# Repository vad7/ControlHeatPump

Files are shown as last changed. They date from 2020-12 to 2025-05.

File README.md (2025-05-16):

# ControlHeatPump
Контроллер теплового насоса

Версия 1.196.<br>
<br>
Проект "Народный контроллер" для тепловых насосов.<br>
Данное програмноое обеспечение предназначено для управления<br>
различными типами тепловых насосов для отопления и ГВС.<br>
<br>
Плата для контроллера, более продробно описана здесь: http://vad-7.blogspot.com/2021/04/HPboard.html
<br>
Гребер и БОМ лист в папке: Arduino DUE shield<br>
<br>
На плате:<br>
1. Разъемы для установки Arduino DUE R3<br>
2. Проводная сеть (W5500) для доступа к контроллеру через интернет<br>
3. Две раздельные линии для цифровых датчиков температуры DS18B20, одна из которых может быть 2-х проводной.<br>
4. Разъем для micro SD карты<br>
5. Флеш-память для веб морды<br>
6. Память 128кбайт для настроек и лога<br>
7. Часы с батарейкой CR2032<br>
8. Опора точного напряжения для аналоговых входов (нужно переключить режим на Arduino DUE)<br>
9. Подключение символьного дисплея LCD 16x2-20x4, доступен также графический Nextion.<br>
10. ЭРВ с униполярной катушкой<br>
11. 2 входа токовая петля 4-20мА<br>
12. 4 аналоговых входа с делителем напряжения<br>
13. 6 цифровых полностью изолированных входов с раздельным подключением изолированного источника напряжения.<br>
14. 2 аналоговых выхода 0-10V<br>
15. Выход на платы реле (до 12 реле)<br>
16. 1 высокоскоростной ШИМ<br>
17. 2 изолированных DC выхода<br>
18. 4 сериал порта<br>
19. 2 шины I2C<br>
20. 6 неизолированных многоцелевых (включая ШИМ) входов-выходов.<br>
21. Зуммер на 12V<br>
22. Разъем для 4-х кнопок.<br>
<br>
Размер 176x120 мм, Arduino DUE выступает на 16 мм.<br>
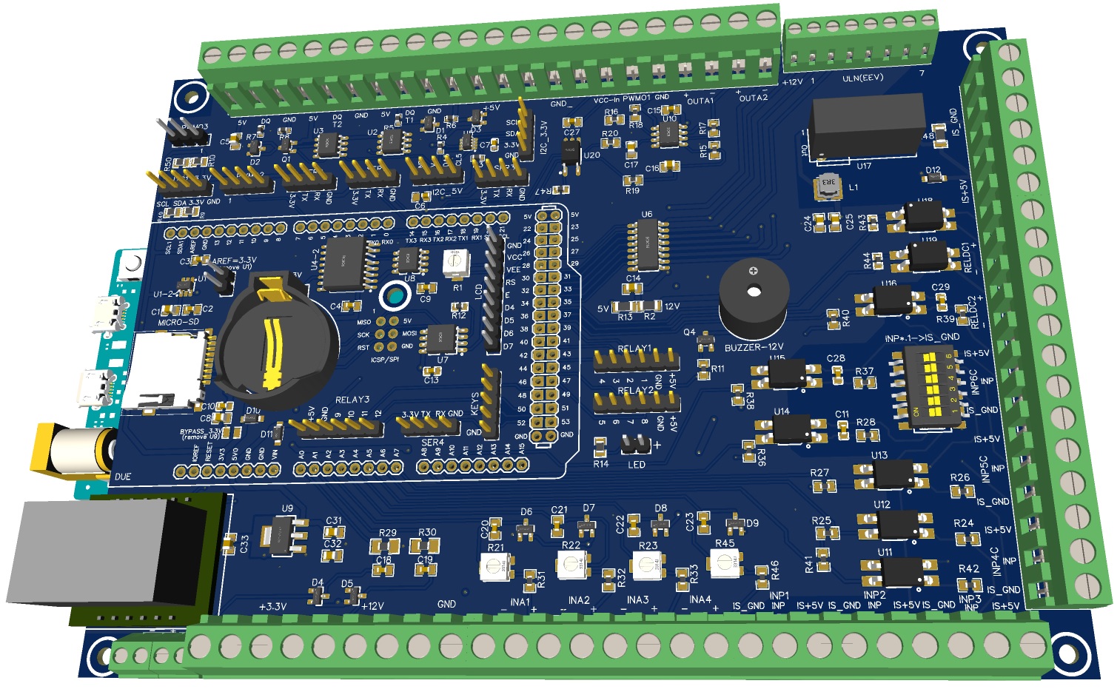
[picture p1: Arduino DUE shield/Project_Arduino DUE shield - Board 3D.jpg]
qr

<br>
<br>
1. Поддержка символьного дисплея 20x4 символов (LCD2004), может работать совместно с Nextion.<br>
2. ТН Воздух-Вода - полная поддержка, установка оборотов компрессора, ЭРВ.<br>
3. Ежесуточные реле - переключение по температуре и по ночному тарифу<br>
4. Дамп ячеек Modbus, загрузка файла дампа в устройство Modbus<br>
5. Частотник Vacon: управление вентилятором, настройка мощности, контроль температуры, авто-сброс ошибки связи<br>
6. Дисплей Nextion: описание ошибки ТН текстом на главном экране, отображение второго уличного датчика, исправление ошибок<br>
7. Исправление множества ошибок в функциях: EEV, WR, Vacon, COP, Pumps, web<br>
8. Корректировка ЭРВ при переходе отопление-бойлер<br>
9. Опция включения циркуляционного насоса ГВС по расписанию<br>
10. Возможность изменять аварийные границы датчиков температур через веб<br>
11. Ограничение оборотов компрессора по времени<br>
12. ГВС: использовать только тэн во время "расписание только для тэна"<br>
13. Не считать статистику с меткой "во время работы" в переходных моментах бойлер-отопление и при возврате масла<br>
14. Статистика - отдельно считается тэн бойлера<br>
15. Пересоздание stats файлов при ошибке последовательности или длине=0<br>
16. Исправление работы насосов в паузе<br>
17. Исправление синхронизации времени, запрет смены часов во время работы ТН<br>
18. Исправление скролбара в веб<br>
19. Опция запрещать смену конкретного расписания<br>
20. Исправление безопасного доступа через веб, из-за кэширования он не работал адекватно<br>
21. Опция продолжения отопления после нагрева бойлера, если внутри гистерезиса<br>
22. Отображение на веб о включении суточных реле<br>
23. Корректировка минимальной мощности ваттроутера в зависимости текущей мощности с MPPT<br>
24. Поддержку двунаправленного электро-счетчика DDS238-2 ZN/S<br>
25. Настройки насосов отопления и дополнительного тэна перенесены в профили<br>
26. Новый режим работы дополнительного тэна на выходе ТН - интеллектуальный, теперь их три: по дому, по улице, интеллектуально<br>
27. Температура цели бойлера на схеме<br>
28. Корректировка датчиков WiFi (esp8266)<br>
29. Нагрев бойлера во время отсутствия электричества, если есть солнце<br>
30. Перенос настройки выключения насоса после останова компрессора в профили, отдельная задача по управлению насосами, чтобы была возможность контроля температур цели.<br>
31. Автопереключение режима работы - Отопление / Охлаждение<br>
32. Возможность использовать несколько периодов включения одного и того же ежесуточного реле.<br>
33. Возможность задать дополнительно любой датчик температуры как цель отопления. Расписание по часам контроля этих датчиков для каждого профиля.<br>
34. Догрев бойлера тэном во время паузы компрессора и низкой температуры или когда не смог нагреть с первого раза.<br>
35. Управление теплым полом по датчикам теплого пола. Два режима - по превышению на заданную дельту целевой температуры или по целевой температуре датчика.<br>
36. Старт нагрева по минимальной температуре подачи.<br>
37. Максимальная температура цели для принудительного останова цикла нагрева, если по другим датчикам еще нужно греть.  <br>
38. Поддержка частотников Danfoss VLT, Danfoss Micro Drive FC-51.<br>
39. Управления дополнительным солнечным подкачивающим инвертором (через реле).<br>
40. Подсчет потребления по дневному/ночному тарифу раздельно, опциональное.<br>

<br><br>

Подробное обсуждение проекта на форуме: <br>
https://www.forumhouse.ru/threads/492563/

Скриншеты веб-интерфейса:

Состояние
Схема
ЭРВ
Настройки
Расписание
Датчики
Реле
Инвертор
RTOS
Графики
Графический лог
Статистика
Ваттроутер

Выносной экран Nextion:

Nextion Main
Nextion Scheme
Nextion Heat

Символьный дисплей LCD2004:



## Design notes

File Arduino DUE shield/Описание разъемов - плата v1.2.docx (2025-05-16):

Входы-выходы НК

№: 1 2 3 4 5 6 7 8 9 10

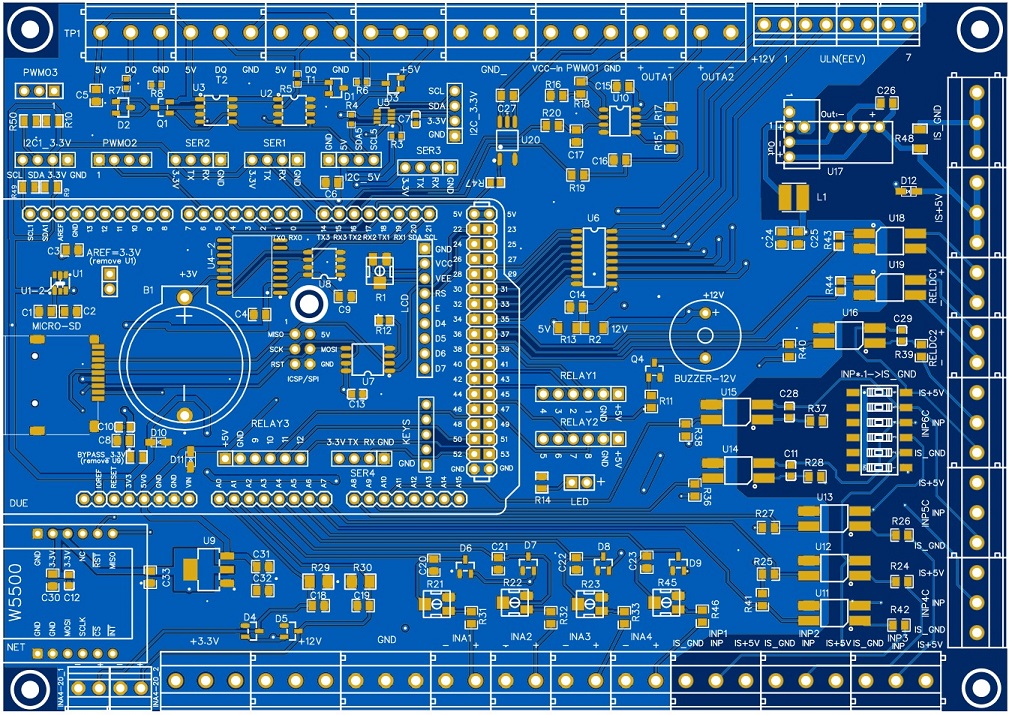
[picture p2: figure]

11

12

13

*

14

MicroSD

15

16

LAN 17

29 28 27 26 25 24 23 22 21 20 19 18

Винтовые разъемы по периметру платы:

1. Датчики температуры DS18B20, двухпроводная или трехпроводная линия (Шина 2)
2. Датчики температуры DS18B20, трехпроводная линия (Шина 1)
3. Датчики температуры DS18B20, трехпроводная линия (Шина 1)
4. Выходы +5V
5. GND (-)
6. Выход изолированный PWM, максимальный ток 8 mA (D5)
7. Выход аналоговый 0-10V (D2)
8. Выход аналоговый 0-10V (D3)
9. ЭРВ (ULN2003), слева на право: +5V или +12V (* - в зависимости от перемычки), D29, D30, D31
10. ЭРВ (ULN2003), слева на право: D32, D33, D34, D35
11. Выход изолированный -5V (GND)
12. Выход изолированный +5V, 1W
13. Реле постоянного тока (оптрон), макс +80V, 50 mA (D36)
14. Реле постоянного тока (оптрон), макс +80V, 50 mA (D37)
15. Вход цифровой изолированный со сглаживающим конденсатором (D38)
16. Вход цифровой изолированный со сглаживающим конденсатором (D64)
17. Вход цифровой изолированный со сглаживающим конденсатором (D63)
18. Вход цифровой изолированный (D62)
19. Вход цифровой изолированный (D61)
20. Вход цифровой изолированный (D60)
21. Вход аналоговый регулируемый R45 (A5/AD2)
22. Вход аналоговый регулируемый R23 (A4/AD3)
23. Вход аналоговый регулируемый R22 (A3/AD4)
24. Вход аналоговый регулируемый R21 (A2/AD5)
25. GND (-)
26. Вход/Выходы +12V
27. Выходы +3.3V
28. Вход аналоговый, токовая петля 4-20 мА, 75 Ом (A1/AD6)
29. Вход аналоговый, токовая петля 4-20 мА, 75 Ом (A0/AD7)

Переключатели INP*.1->IS_GND замыкают выводы IS_GND разъемов №15 - №20 (сверху вниз) на изолированный -5V (GND).

Разъемы на плате:

RELAY1 – Выход на плату реле, 3.3V, контакты 1-4 (D39, D40, D41, D42)

RELAY2 – Выход на плату реле, 3.3V, контакты 5-8 (D44, D45, D46, D47)

RELAY3 – Выход на плату реле, 3.3V, контакты 9-12 (D48, D49, D50, D51)

Платы реле 5V - включение высоким уровнем (High Level Trigger)

KEYS – Кнопки, снизу вверх (GND, D66, D67, D68, D69)

LCD – Цифровой дисплей 20x4 символов, 5V, R1 – регулировка контраста

LED – Зеленый светодиод

SER1 – Порт Serial3, 3.3V

SER2 – Порт Serial2, 3.3V

SER3 – Порт Serial1, 3.3V

SER4 – Порт Serial4, 3.3V

I2C_3.3V – Шина I2C 3.3V (I2C)

I2C_5V – Шина I2C 5V (I2C)

I2C1_3.3V – Вторая шина I2C 3.3V (I2C1)

PWM02 – Выходы/Входы МК 3.3V, 9 мА, доступен PWM (GND, D6, D7, D9)

PWM03 – Выходы/Входы МК 3.3V, 9 мА (D13 – 3 мА), доступен PWM (D11, D12, D13[LED])

B1 – Батарейка CR2032, 3V

Датчики токовая петля 4-20 мА 12V подключаются так:

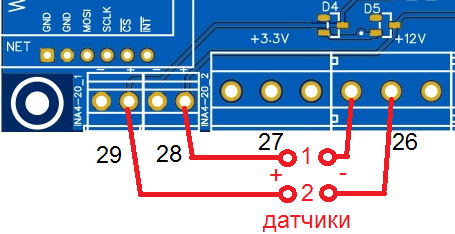
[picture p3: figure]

Доработка китайской платы Arduino DUE R3:

1. Припять резистор поверхностного монтажа (0603 размер) номиналом 10 кОм между ERASE линией и + 3,3В (на ножки транзистора).

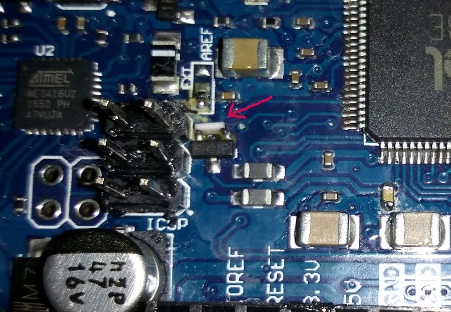
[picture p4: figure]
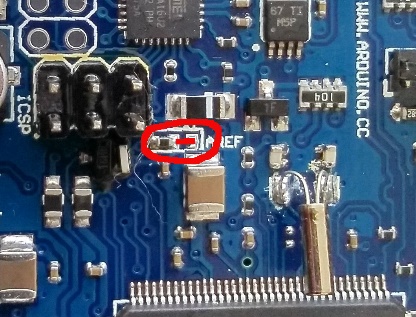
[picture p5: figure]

2. Перепаять перемычку AREF с левых контактов на правые – внешняя опора AREF.

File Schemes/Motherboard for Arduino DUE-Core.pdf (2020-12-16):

Платы 100x100мм.
Главная плата питается от 5V. Для аналогового выхода есть возможность подключить другое напряжение.
На плате места для:
1. платы часов (ZS_042)
2. платы сети W5500 lite (USR-ES1)
3. платы MicroSD 5V
4. разъем MicroSD
5. 3-х узких плат RS485 - TTL или других Serial-устройств.
6. 2 платы для датчиков температуры DS18B20 или других I2C устройств
7. дисплея LCD2004 (1602)
8. 4-х кнопок
9. Вторая шина I2C.

Входы-выходы:
1. два токовых входа (4-20 мА)
2. три аналоговых входа с подстройкой
3. два аналоговых выхода (LM358)
4. 18 цифровых выходов, включая 7 от ULN2003 для ЭРВ
5. 6 цифровых входов
6. Выход 5V через транзистор для пищалки, сирены или т. п.
Клеммники с шагом 5мм (KF128/129-5.08), на пищалку с шагом 3.5мм (KF350-3.5)

Плата реле реле подключается 20 пиновым двурядным шлейфом с шагом 2.54 мм (JTAG 2.54mm 20 pin).
На плату подается с внешнего источника высокое напряжение (12-24V и/или 5V) от них питаются ULN и реле.
На плате:
1. 6 развязанных через оптрон цифровых входа (клеммник KF350-3.5)
2. 5 твердотельных реле: оптосимистор + симистор BTA16 (16A), один можно воткнуть BTA41 (41A). (KF129-5.08)
3. 1 обычное реле на 16A, переключающие контакты (Omron G2RL-1-E или аналог) (KF129-5.08)
4. два выхода через оптрон, один можно сделать аналоговым через PWM. (KF350-3.5)
5. ULN2003 для управления ЭРВ или типа того (KF350-3.5)

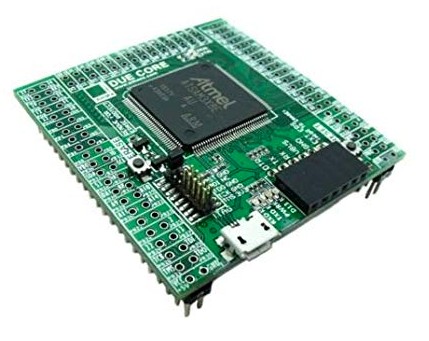
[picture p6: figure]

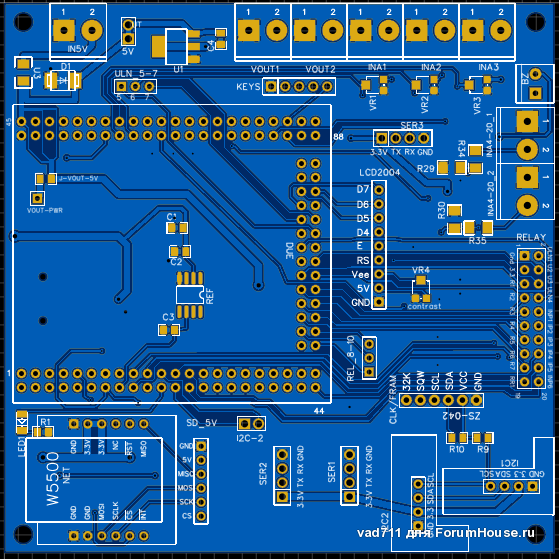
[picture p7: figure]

Плата реле:

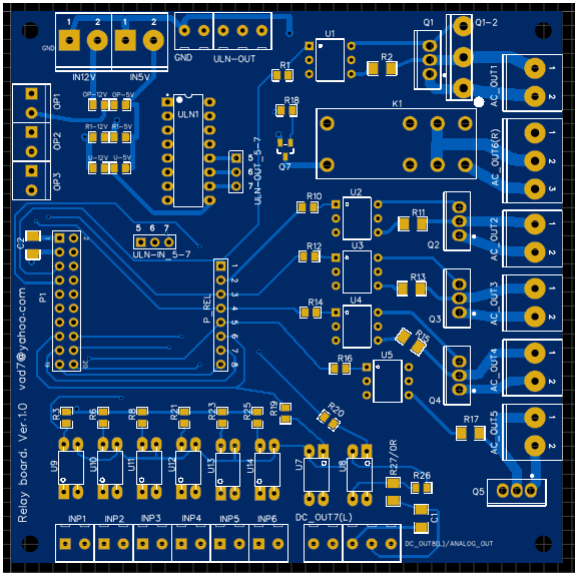
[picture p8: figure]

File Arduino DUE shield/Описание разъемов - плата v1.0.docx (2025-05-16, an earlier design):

Входы-выходы НК

№: 1 2 3 4 5 6 7 8 9 10 11

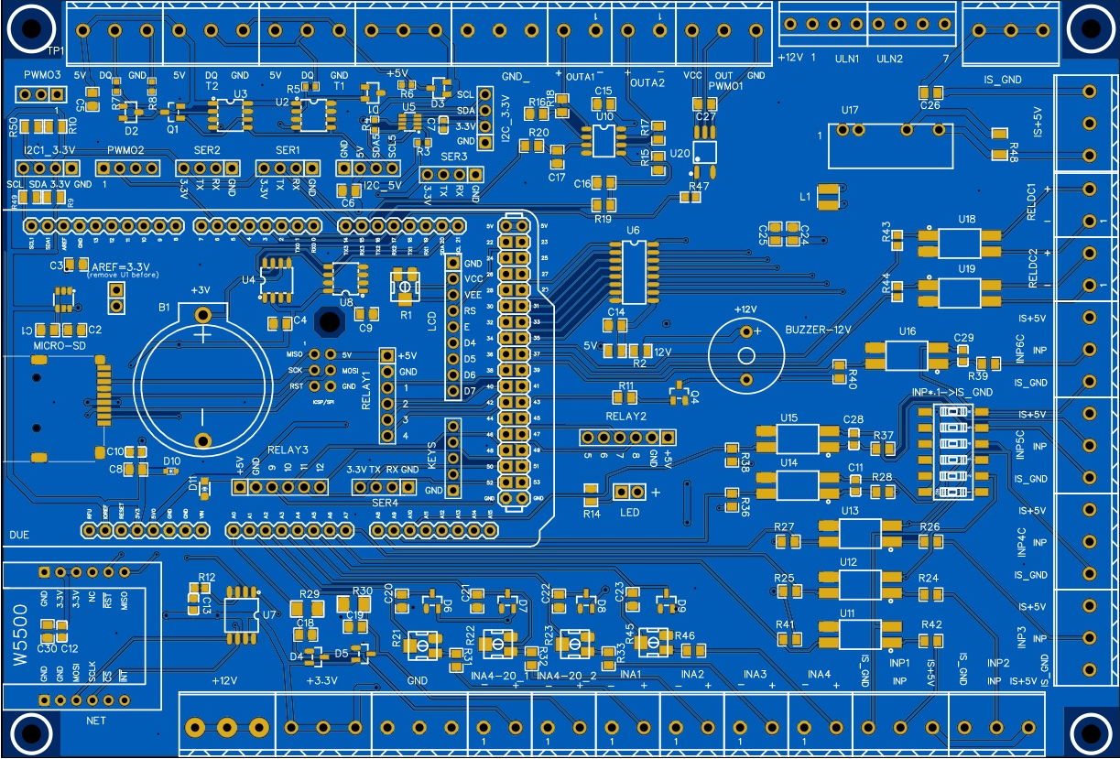
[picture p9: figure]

12

13

14

*

15

MicroSD

16

17

LAN 18

29 28 27 26 25 24 23 22 21 20 19

Винтовые разъемы по периметру платы:

1. Датчики температуры DS18B20, двухпроводная или трехпроводная линия (Шина 2)
2. Датчики температуры DS18B20, трехпроводная линия (Шина 1)
3. Датчики температуры DS18B20, трехпроводная линия (Шина 1)
4. Выходы +5V
5. GND (-)
6. Выход аналоговый 0-10V (D2)
7. Выход аналоговый 0-10V (D3)
8. Выход изолированный PWM, максимальный ток 8 mA (D5)
9. ЭРВ (ULN2003), слева на право: +5V или +12V (* - в зависимости от перемычки), D29, D30, D31
10. ЭРВ (ULN2003), слева на право: D32, D33, D34, D35
11. Выход изолированный -5V (GND)
12. Выход изолированный +5V, 1W
13. Реле постоянного тока (оптрон), макс +80V, 50 mA (D36)
14. Реле постоянного тока (оптрон), макс +80V, 50 mA (D37)
15. Вход цифровой изолированный со сглаживающим конденсатором (D38)
16. Вход цифровой изолированный со сглаживающим конденсатором (D64)
17. Вход цифровой изолированный со сглаживающим конденсатором (D63)
18. Вход цифровой изолированный (D62)
19. Вход цифровой изолированный (D61)
20. Вход цифровой изолированный (D60)
21. Вход аналоговый регулируемый R45 (A5/AD2)
22. Вход аналоговый регулируемый R23 (A4/AD3)
23. Вход аналоговый регулируемый R22 (A3/AD4)
24. Вход аналоговый регулируемый R21 (A2/AD5)
25. Вход аналоговый, токовая петля 4-20 мА, 75 Ом (A1/AD6)
26. Вход аналоговый, токовая петля 4-20 мА, 75 Ом (A0/AD7)
27. GND (-)
28. Выходы +3.3V
29. Вход/Выходы +12V

Переключатели INP*.1->IS_GND замыкают выводы IS_GND разъемов №15 - №20 (сверху вниз) на изолированный -5V (GND).

Разъемы на плате:

RELAY1 – Выход на плату реле, 3.3V, контакты 1-4 (D39, D40, D41, D42)

RELAY2 – Выход на плату реле, 3.3V, контакты 5-8 (D44, D45, D46, D47)

RELAY3 – Выход на плату реле, 3.3V, контакты 9-12 (D48, D49, D50, D51)

Платы реле 5V - включение высоким уровнем (High Level Trigger)

KEYS – Кнопки, снизу вверх (GND, D66, D67, D68, D69)

LCD – Цифровой дисплей 20x4 символов, 5V, R1 – регулировка контраста

LED – Зеленый светодиод

SER1 – Порт Serial3, 3.3V

SER2 – Порт Serial2, 3.3V

SER3 – Порт Serial1, 3.3V

SER4 – Порт Serial4, 3.3V

I2C_3.3V – Шина I2C 3.3V (I2C)

I2C_5V – Шина I2C 5V (I2C)

I2C1_3.3V – Вторая шина I2C 3.3V (I2C1)

PWM02 – Выходы/Входы МК 3.3V, 9 мА, доступен PWM (GND, D6, D7, D9)

PWM03 – Выходы/Входы МК 3.3V, 9 мА (D13 – 3 мА), доступен PWM (D11, D12, D13[LED])

B1 – Батарейка CR2032, 3V

Датчики токовая петля 4-20 мА 12V подключаются так:

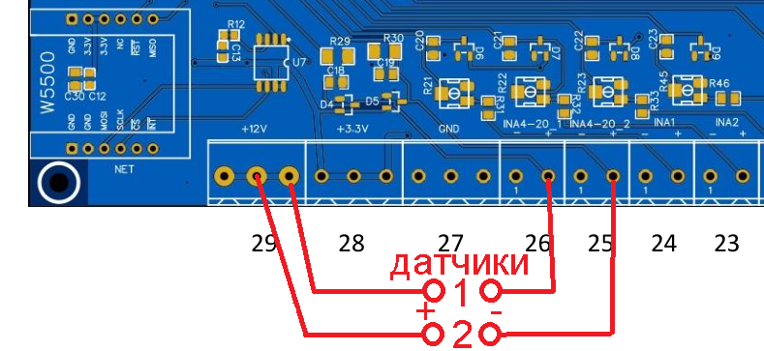
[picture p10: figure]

Доработка китайской платы Arduino DUE R3:

1. Припять резистор поверхностного монтажа (0603 размер) номиналом 10 кОм между ERASE линией и + 3,3В (на ножки транзистора).


2. Перепаять перемычку AREF с левых контактов на правые – внешняя опора AREF.

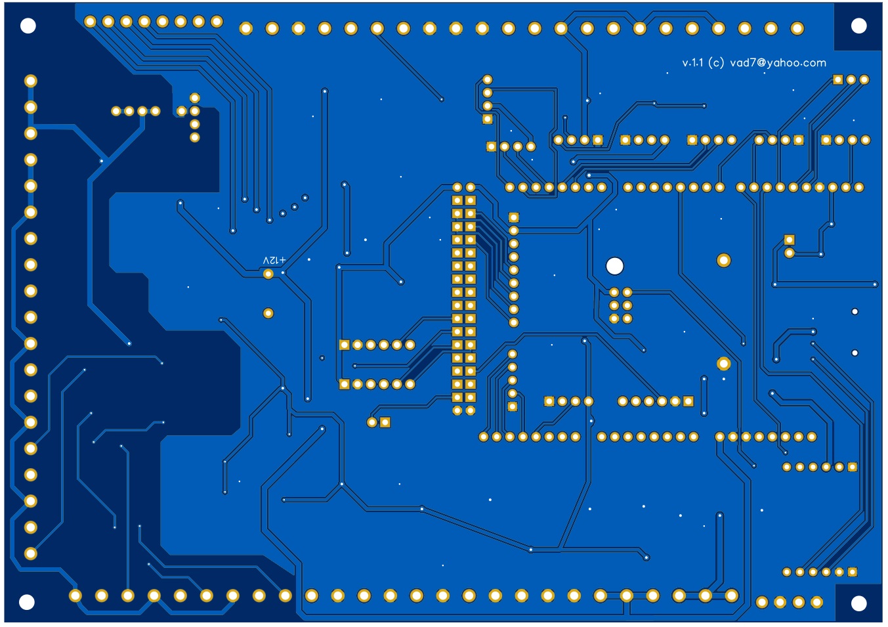
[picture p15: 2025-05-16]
Arduino DUE shield/Project_Arduino DUE shield - Board 2D_2.jpg

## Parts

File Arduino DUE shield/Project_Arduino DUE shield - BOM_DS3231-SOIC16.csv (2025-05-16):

ID | Name | Designator | Footprint | Quantity | Manufacturer Part | Manufacturer | Supplier | Supplier Part | Mounted | LCSC Assembly | JLCPCB SMD | Assembly Type | Paste Type
1 | CR2032-BS-2-1 | B1 | BAT-TH_BS-2-1 | 1 | BS-2-1 | Q&J | LCSC | C70376
2 | TMB12A12 | BUZZER-12V | BUZ-TH_BD12.0-P7.60-D0.6-FD | 1 | TMB12A12 | HNDZ | LCSC | C96079 |  | Yes
3 | 10u | C5 | C_805 | 1 | CL21A106KAYNNNE | SAMSUNG | LCSC | C15850 | Yes
4 | 0.1u | C6,C7 | C0603 | 2 | CC0603KRX7R9BB104 | YAGEO | LCSC | C14663 | Yes
5 | 0.1u | C2,C3,C4,C9,C10,C12,C13,C15,C26,C27 | C0603 | 10 | CC0603KRX7R9BB104 | YAGEO | LCSC | C14663
6 | 10u | C1,C8,C14,C16,C17,C24,C25,C30,C31,C32,C33 | C_805 | 11 | CL21A106KAYNNNE | SAMSUNG | LCSC | C15850
7 | 0.01u | C11,C18,C19,C20,C21,C22,C23,C28,C29 | C0603 | 9 | 0603B103K500NT | FH | LCSC | C57112
8 | PACDN042Y3R | D1,D2,D3 | SOT-23-3_L3.0-W1.7-P0.95-LS2.9-BR | 3 | PACDN042Y3R | ON Semicon | LCSC | C233486 |  | Yes
9 | BAT54SLT1G | D4,D5,D6,D7,D8,D9 | SOT-23_L2.9-W1.3-P1.90-LS2.4-BR | 6 | BAT54SLT1G | ON | LCSC | C19726 |  |  | Yes
10 | UCLAMP3301H.TCT | D10 | SOD123-SOD523 | 1 | UCLAMP3301H.TCT | SEMTECH | LCSC | C117558 |  | Yes | Yes | smtWeld | expand
11 | DESD5V0U1BA-7 | D11,D12 | SOD123-SOD523 | 2 | DESD5V0U1BA-7 | Diodes Incorporated | LCSC | C460442
12 | PA_DUE_BRD | DUE | PA_DUE 1 HOLE | 1 | ?
13 | A2541WV-4P | I2C1_3.3V,I2C_3.3V | HDR-TH_4P-P2.54-V I2C 3.3V | 2 | A2541WV-4P | Changjiang Connectors | LCSC | C225479 |  | Yes
14 | A2541WV-4P | I2C_5V | HDR-TH_4P-P2.54-V I2C 5V | 1 | A2541WV-4P | Changjiang Connectors | LCSC | C225479 |  | Yes
15 | KF128L-5.08-2P | INA1,INA2,INA3,INA4,RELDC1,RELDC2 | CONN-TH_P5.08_KF128L-5.08-2P SIGN | 6 | KF128L-5.08-2P | Cixi Kefa Elec | LCSC | C474940 |  | Yes
16 | KF128L-3.5-2P | INA4-20_1,INA4-20_2 | CONN-TH_P3.50_KF128L-3.5-2P SIGN | 2 | KF128L-3.5-2P | Cixi Kefa Elec | LCSC | C474930 |  | Yes |  | manualWeld | expand
17 | KF128L-5.08-3P | INP1,INP2,INP3,INP4C,INP5C,INP6C | CONN-TH_3P-P5.08_KF128L-5.08-3P INP | 6 | KF128L-5.08-3P | Cixi Kefa Elec | LCSC | C474941 |  | Yes
18 | EM-06-Q | INP*.1->IS_GND | SW-SMD_12P-L15.1-W6.0-P2.54-LS9.8 | 1 | EM-06-Q | Diptronics | LCSC | C501580 |  | Yes |  | smtWeld | expand
19 | KF128L-5.08-3P | +3.3V,+5V,+12V,GND,GND_,IS+5V,IS_GND,PWMO1 | CONN-TH_3P-P5.08_KF128L-5.08-3P | 8 | KF128L-5.08-3P | Cixi Kefa Elec | LCSC | C474941 |  | Yes
20 | A2541WV-5P | KEYS | HDR-TH_5P-P2.54-V | 1 | A2541WV-5P | Changjiang Connectors | LCSC | C225480 |  | Yes
21 | 10uH | L1 | IND-SMD_3.0-4.0W | 1 | FNR4018S100MT | cjiang | LCSC | C167808
22 | PZ254V-11-09P | LCD | HDR-TH_9P-P2.54-V-M LCD | 1 | PZ254V-11-09P | XFCN | LCSC | C492408 |  | Yes
23 | TF-01A | MICRO-SD | TF-SMD_TF-01A | 1 | TF-15×15 | SOFNG | LCSC | C111196
24 | W5500 module | NET | W5500_MODULE | 1 | ?
25 | KF128L-5.08-2P | OUTA1,OUTA2 | CONN-TH_P5.08_KF128L-5.08-2P SIGN | 2 | KF128L-3.5-2P | Cixi Kefa Elec | LCSC | C474930 |  | Yes
26 | A2541WV-4P | PWMO2 | HDR-TH_4P-P2.54-V | 1 | A2541WV-4P | Changjiang Connectors | LCSC | C225479 |  | Yes
27 | A2541WV-3P | PWMO3 | HDR-TH_3P-P2.54-V-M | 1 | A2541WV-3P | Changjiang Connectors | LCSC | C225478 |  | Yes
28 | BSS84LT1G | Q1 | SOT-23-3_L2.9-W1.6-P1.90-LS2.8-BR | 1 | LBSS84LT1G | LRC | LCSC | C8492 |  | Yes | Yes
29 | BC817-25LT1G | Q4 | SOT-23-3_L2.9-W1.6-P1.90-LS2.8-BR | 1 | BC817-25LT1G | ON | LCSC | C82635 |  | Yes | Yes
30 | 10K | R1,R21,R22,R23,R45 | RES-ADJ-SMD_3314J | 5 | 3314J-1-103E | BOURNS | LCSC | C36376 |  | Yes
31 | 3.9k | R3,R4 | R0603 | 2 | 0603WAF3901T5E | UniOhm | LCSC | C23018 | Yes
32 | 5 | R5,R6,R7,R8 | R0603 | 4 | 0603WAF510KT5E | UniOhm | LCSC | C25197
33 | 1k | R9,R10,R49,R50 | R0805 | 4 | 0603WAF1001T5E | UniOhm | LCSC | C21190
34 | 10K | R11 | R0603 | 1 | 0603WAF1002T5E | UniOhm | LCSC | C25804
35 | 10k | R15,R16,R19,R20 | R0603 | 4 | 0603WAF1002T5E | UniOhm | LCSC | C25804
36 | 22k | R17,R18 | R0603 | 2 | 0603WAF2202T5E | UniOhm | LCSC | C31850
37 | 75 | R29,R30 | R0805 | 2 | 0805W8F750JT5E | UniOhm | LCSC | C20638
38 | 6.8k | R31,R32,R33,R46 | R0603 | 4 | 0603WAF6801T5E | UniOhm | LCSC | C23212
39 | 4.7k | R25,R27,R36,R38,R40,R41 | R0603 | 6 | 0603WAF4701T5E | UniOhm | LCSC | C23162
40 | 1k | R12,R24,R26,R28,R37,R39,R42,R43,R44 | R0603 | 9 | 0603WAF1001T5E | UniOhm | LCSC | C21190
41 | 330 | R14,R47 | R0603 | 2 | 0603WAF3300T5E | UniOhm | LCSC | C23138
42 | 300 | R48 | R1206 | 1 | 1206W4F3000T5E | UniOhm | LCSC | C17887 |  | Yes | Yes
43 | Header-Male-2.54_1x6 | RELAY1 | HDR-TH_6P-P2.54-V R5V1 | 1 | Header-Male-2.54_1x6 | BOOMELE | LCSC | C37208 |  | Yes
44 | Header-Male-2.54_1x6 | RELAY2 | HDR-TH_6P-P2.54-V R5V2 | 1 | Header-Male-2.54_1x6 | BOOMELE | LCSC | C37208 |  | Yes
45 | Header-Male-2.54_1x6 | RELAY3 | HDR-TH_6P-P2.54-V R5V3 | 1 | Header-Male-2.54_1x6 | BOOMELE | LCSC | C37208 |  | Yes
46 | A2541WV-4P | SER1,SER2,SER3,SER4 | HDR-TH_4P-P2.54-V SERIAL | 4 | A2541WV-4P | Changjiang Connectors | LCSC | C225479 |  | Yes
47 | KF128L-5.08-3P | T1,T2,TP1 | CONN-TH_3P-P5.08_KF128L-5.08-3P DS18B20 | 3 | KF128L-5.08-3P | Cixi Kefa Elec | LCSC | C474941 |  | Yes
48 | REF3030AIDBZR | U1-2 | SOT-23-3_L2.9-W1.6-REF | 1 | REF3030AIDBZR | TI | LCSC | C38423 |  |  | Yes | smtWeld | recommend
49 | DS2482S-100+TR | U2,U3 | SOIC-8_L4.9-W3.9-P1.27-LS6.0-BL | 2 | DS2482S-100+T&R | MAXIM | LCSC | C143306 |  | Yes | Yes
50 | DS3231M+TRL | U4-2 | SOIC-16_L10.3-W7.5-P1.27-LS10.3-BL NO_UNUSED_PIN | 1 | DS3231M+TRL | MAXIM | LCSC | C37663
51 | MAX3373EEKA+T | U5 | SOT-23-8_L3.0-W1.7-P0.65-LS2.8-TL THIN PADS | 1 | MAX3373EEKA+T | Maxim Integrated | LCSC | C116658 |  | Yes | Yes
52 | ULN2003D1013TR | U6 | SOIC-16_L9.9-W3.9-P1.27-LS6.0-BL | 1 | ULN2003ADR | TI | LCSC | C7512 |  | Yes | Yes
53 | MX25L3206EM2I-12G | U7 | SOIC-8_L5.3-W5.3-P1.27-LS8.0-BL | 1 | MX25L3206EM2I-12G | Micronix | LCSC | C16142 |  | Yes | Yes
54 | M24M01-RMN6TP | U8 | SOIC-8_L4.9-W3.9-P1.27-LS6.0-BL | 1 | M24M01-RMN6TP | STMicroelectronics | LCSC | C79990 |  | Yes | Yes
55 | LM1117MPX-3.3/NOPB | U9 | SOT-223-3_L6.5-W3.4-P2.30-LS7.0-BR | 1 | LM1117IMPX-3.3/NOPB | TI | LCSC | C23984 |  | Yes | Yes | smtWeld | expand
56 | LM358DR2G | U10 | SOIC-8_L5.0-W4.0-P1.27-LS6.0-BL | 1 | LM358DR2G | ON | LCSC | C7950 |  | Yes | Yes
57 | PC817X3NIP1B | U11,U12,U13,U14,U15,U16,U18,U19 | OPTO-SMD-4_L4.6-W6.5-P2.54_SOP-4-L3.9-W4.4 | 8 | EL357N(C)(TA)-G | EVERLIGHT | LCSC | C29981 |  |  | Yes
58 | IF1205S-2W | U17 | PWRM-TH_L11.6-19.6 | 1 | IF1205S-2W | Bothhand Enterprise | LCSC | C494963
59 | TLP104(TPL,E | U20 | SOP-6_5P-L4.4-W3.6-P1.27-LS7.0-BR-PE2 | 1 | TLP104(TPL,E | TOSHIBA | LCSC | C48236 |  | Yes | Yes
60 | KF128L-3.5-2P | ULN(EEV),ULN(EEV)1,ULN(EEV)2,ULN(EEV)3 | CONN-TH_P3.50_KF128L-3.5-2P CORR | 4 | KF128L-3.5-2P | Cixi Kefa Elec | LCSC | C474930 |  | Yes |  | manualWeld | expand

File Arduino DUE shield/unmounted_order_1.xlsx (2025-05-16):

R2,R13 | 0 | R1206 | Part Number:0 footprint name:R1206 [string length must be less or equal than 1 character] | 2
AREF=3.3V,LED | A2541WV-2P | HDR-TH_P2.54-H-M_A2541WV-2P | 2
PWMO3 | A2541WV-3P | HDR-TH_3P-P2.54-V-M | No part matched | 1
I2C1_3.3V,I2C_3.3V | A2541WV-4P | HDR-TH_4P-P2.54-VI2C3.3V | 2
I2C_5V | A2541WV-4P | HDR-TH_4P-P2.54-VI2C5V | 1
PWMO2 | A2541WV-4P | HDR-TH_4P-P2.54-V | 1
SER1,SER2,SER3,SER4 | A2541WV-4P | HDR-TH_4P-P2.54-VSERIAL | 4
KEYS | A2541WV-5P | HDR-TH_5P-P2.54-V | 1
U1 | ADR3430ARJZ-R7 | SOT-23-6_L2.9-W1.6-P0.95-LS2.8-TL | 1
B1 | CR2032-BS-2-1 | BAT-TH_BS-2-1 | No part matched | 1
D11 | DESD5V0U1BA-7 | SOD-323_L1.8-W1.3-LS2.5-BI | No part matched | 1
RELAY2 | Header-Male-2.54_1x6 | HDR-TH_6P-P2.54-VR5V2 | 1
RELAY3 | Header-Male-2.54_1x6 | HDR-TH_6P-P2.54-VR5V3 | 1
RELAY1 | Header-Male-2.54_1x6 | HDR-TH_6P-P2.54-VR5V1 | 1
U17 | IF1205S-2W | PWRM-TH_IFXXXXS-2W | No part matched | 1
Designator | Name | Footprint | Quantity
DUE | PA_DUE_BRD | PA_DUE1HOLE | No part matched | 1
LCD | PZ254V-11-09P | HDR-TH_9P-P2.54-V-MLCD | 1
MICRO-SD | TF-01A | TF-SMD_TF-01A | No part matched | 1
BUZZER-12V | TMB12A12 | BUZ-TH_BD12.0-P7.60-D0.6-FD | 1
D10 | UCLAMP3301H.TCT | SOD-523_L1.2-W0.8-LS1.6-BI | 1
NET | W5500module | W5500_MODULE | No part matched | 1
INA1,INA2,INA3,INA4,INA4-20_1,INA4-20_2,OUTA1,OUTA2,RELDC1,RELDC2 | WJ500V-5.08-2P-14-00A | CONN-TH_2P-P5.00_WJ500V-5.08-2P-+ | 10
GND_,IS+5V,IS_GND | WJ500V-5.08-3P-14-00A | CONN-TH_3P-P5.00_WJ500V-5.08-3P | 3
+3.3V,+5V,+12V,GND | WJ500V-5.08-3P-14-00A | CONN-TH_3P-P5.00_WJ500V-5.08-3P | 4
T1,T2,TP1 | WJ500V-5.08-3P-14-00A | CONN-TH_3P-P5.00_WJ500V-5.08-3PDS18B20 | 3
PWMO1 | WJ500V-5.08-3P-14-00A | CONN-TH_3P-P5.00_WJ500V-5.08-3PPWMO | 1
INP1,INP2,INP3,INP4C,INP5C,INP6C | WJ500V-5.08-3P-14-00A | CONN-TH_3P-P5.00_WJ500V-5.08-3PINP | 6 | 17
ULN1,ULN2 | XY350V-3.5-4P | CONN-TH_XY350V-3.5-4P | 2 | 2 | 3*2+2*1
верх | 9+6+7+3=25
справа | 10+9=19
низ | 9+12+6=27
12 | 1
10 | 1
9 | 3
6 | 2
7 | 1
3 | 1

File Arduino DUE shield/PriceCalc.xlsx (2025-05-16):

 | Board Qty | Cost, $
PCB manufacturing | 10 | 320
LCSC parts | 10 | 75
LCSC parts | 10 | 25
Aliexpress parts | 10 | 60
Aliexpress parts (W5500) | 10 | 40
пайка разъемов | 10 | 180
 |  | 700 | 52500

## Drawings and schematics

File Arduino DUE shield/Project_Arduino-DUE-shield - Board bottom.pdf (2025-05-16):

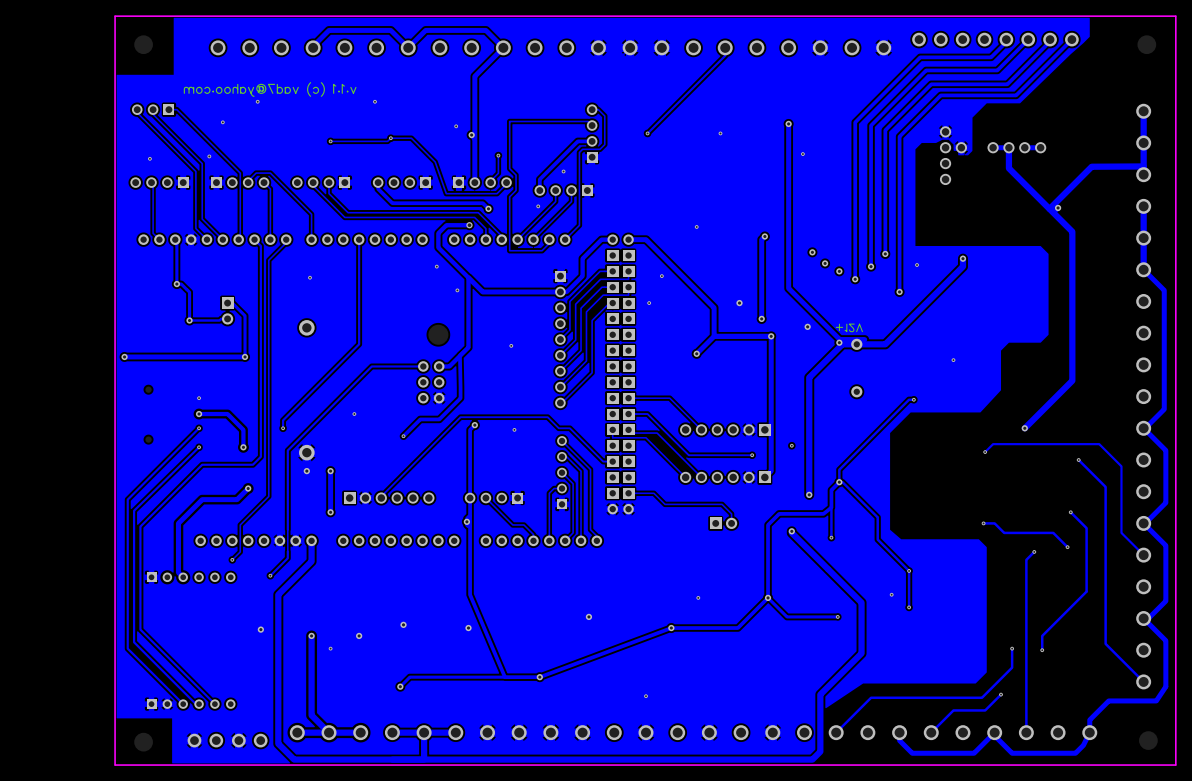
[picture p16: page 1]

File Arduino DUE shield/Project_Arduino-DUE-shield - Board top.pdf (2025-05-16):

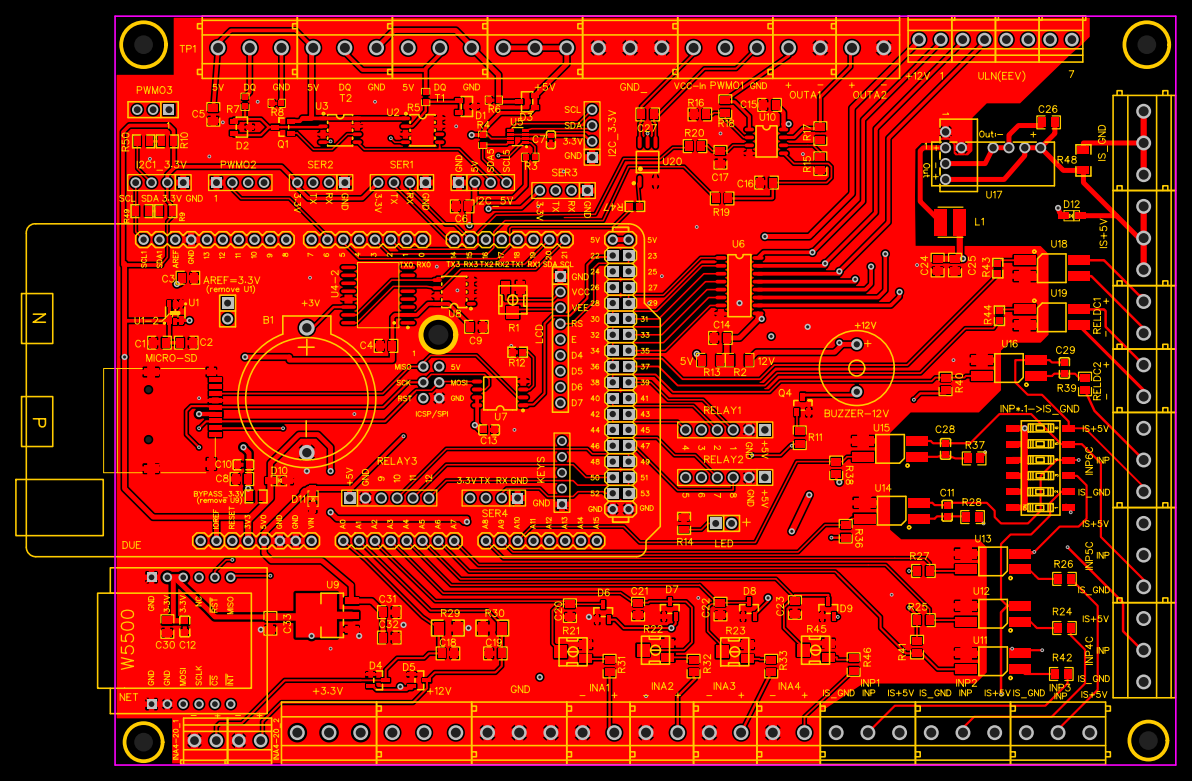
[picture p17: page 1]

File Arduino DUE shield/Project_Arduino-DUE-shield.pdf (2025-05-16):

(TX0)1 | 1 2 | 2 3 | 3 4 | 4 5 | 5 6 | 6 7 | 7 8 | 8 9 | 9 10 | 10

W5500

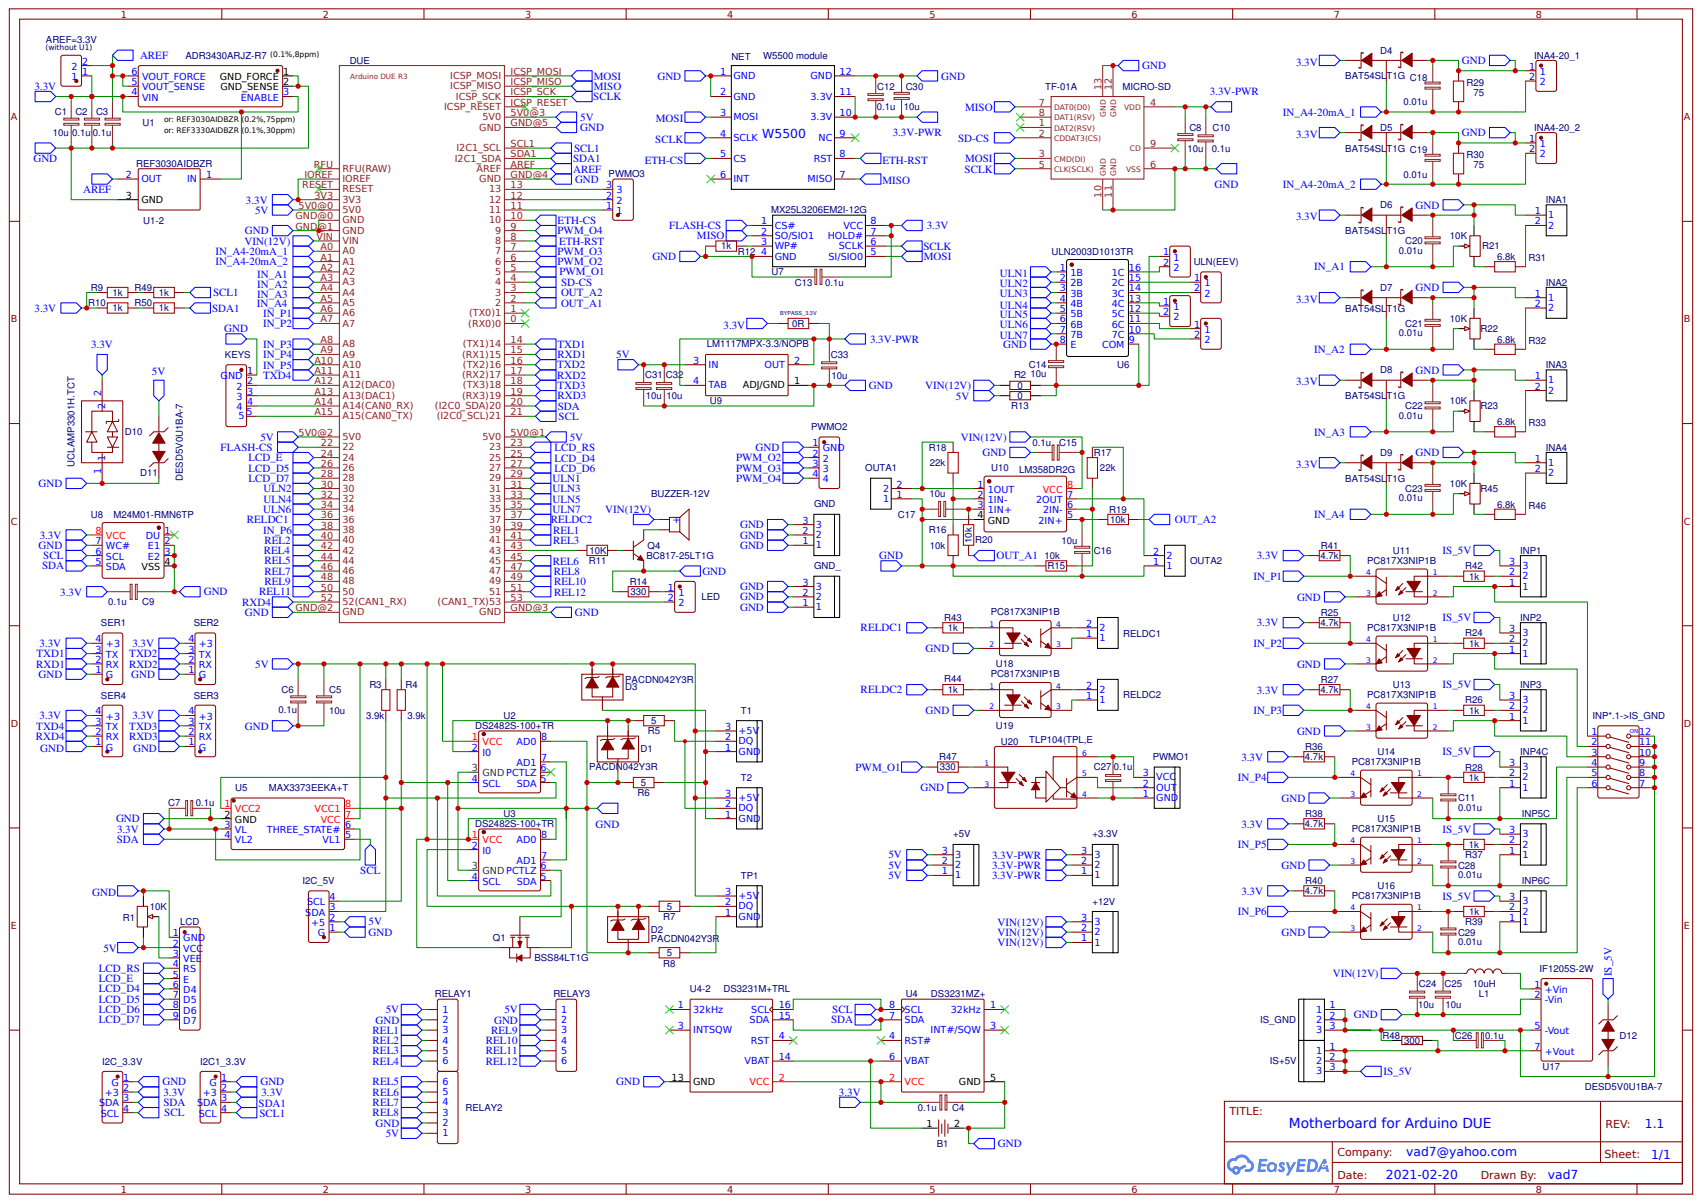
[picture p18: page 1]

U8 M24M01-RMN6TP
VSS 4 SDA 5 SCL 6 WC# 7 VCC 8

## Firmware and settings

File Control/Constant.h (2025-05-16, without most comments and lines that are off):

#define Constant_h
#include "Config.h"                         // Цепляем сразу конфигурацию
#include "Util.h"
#define VERSION			"1.196"				// Версия прошивки
#define VER_SAVE		158					// Версия формата данных в I2C памяти, при изменении добавить размеры структур в HP.Prof.convert_to_new_version() !!!
#define UART_SPEED		115200				// Скорость отладочного порта
#ifdef DEBUG_NATIVE_USB                    // Куда выводить отладку
#define SerialDbg	SerialUSB
#else
#define SerialDbg	Serial
#endif
#define FAST_LIB                            // использование допиленной библиотеки езернета Обычно используется
#define TIME_ZONE         3                 // поправка на часовой пояс по ДЕФОЛТУ
#define NTP_SERVER        "time.nist.gov"   // NTP сервер для синхронизации времени по ДЕФОЛТУ (готовимся к отключению буржуинского инета - "ntp2.stratum2.ru")
#define NTP_SERVER_LEN    60                // максимальная длиная адреса NTP сервера
#define NTP_PORT		  123
#define NTP_LOCAL_PORT    8888              // локальный порт, который будет прослушиваться на предмет UDP-пакетов NTP сервера
#define NTP_REPEAT        3                 // Число попыток запросов NTP сервера
#define NTP_REPEAT_TIME   1000              // (мсек) Время между повторами ntp пакетов
#define PING_SERVER       "192.168.0.1"     // ping сервер по ДЕФОЛТУ
#define WDT_TIME          10                // период Watchdog таймера секунды но не более 16 секунд!!! ЕСЛИ установить 0 то Watchdog будет отключен!!!
#define INDEX_FILE        "index.html"       // стартовый файл по умолчанию для большой морды
#define INDEX_MOB_FILE    INDEX_FILE         // стартовый файл по умолчанию для мобильной морды
#define MOB_PATH          "/mob/"            // Путь к мобильной морде
const char HEADER_BIN[] = "HP-SAVE-DATA";   // Заголовок (начало) файла при сохранении настроек. Необходим для поиска данных в буфере данных при восстановлении из файла
#define MAX_LEN_PM        250               // максимальная длина строкового параметра в запросе (расписание бойлера 175 байт) кодирование описания профиля 40 букв одна буква 6 байт (двойное кодирование)
#define CHART_POINT       300               // Максимальное число точек графика, одна точка это 2 байта * число графиков  //300 - работает
#define ADC_PRESCAL       2					// ADCClock = MCK / ( (PRESCAL+1) * 2 )
#define TARIF_NIGHT_START 23				// Начальный час ночного тарифа электроэнергии
#define TARIF_NIGHT_END   7					// Ночной тариф электроэнергии заканчивается в
byte defaultMAC[] = { 0xDE, 0xA1, 0x1E, 0x01, 0x02, 0x03 };// не менять
const uint16_t  defaultPort=80;
#define GETBIT(b,f)   ((b&(1<<(f)))?true:false)              // получить состяние бита
#define SETBIT1(b,f)  (b|=(1<<(f)))                          // установка бита в 1
#define SETBIT0(b,f)  (b&=~(1<<(f)))                         // установка бита в 0
#define ALIGN(a) ((a + 3) & ~3)
#define SD_REPEAT         3                 // Число попыток чтения карты, открытия файлов, при неудаче переход на работу без карты
#define W5200_THREAD      3                 // Число потоков для сетевого чипа w5200 допустимо 1-4 потока, на 4 скорее всего не хватить места в оперативке
#define W5200_NUM_PING    4                 // Число попыток пинга до определения потери связи
#define W5200_TIME_PING   1000              // мсек Время между попытками пинга (если не удача)
#define W5200_MAX_LEN     2048 //=W5100.SSIZE // Максимальная длина буфера, определяется W5200 не более 2048 байт
#define W5200_NUM_LINK    2                 // Число попыток сброса чипа w5500 и проверки появления связи (кабель воткнут) используется для инициализаци чипа
#define W5200_TIME_LINK   4000              // Максимальное время ожидания устанoвления связи (поднятие Link) кабель воткнут  используется для инициализаци чипа (мсек)
#define W5200_TIME_WAIT   3000              // Время ожидания захвата мютекса (переключение потоков) мсек
#define W5200_SPI_SPEED   SPI_RATE          // ЭТО ДЕЛИТЕЛЬ (SPI_RATE определен в w5100.h)!!! Частота SPI w5200 = 84/W5200_SPI_SPEED т.е. 2-42МГц 3-28МГц 4-21МГц 6-14МГц Диапазон 2-6
#define W5200_SOCK_SYS    (MAX_SOCK_NUM-1)  // Номер системного сокета который не использутся в вебсервере, это последний сокет, НЕ МЕНЯТЬ
#define W5200_RTR         (2*0x07D0)        // время таймаута в 100 мкс интервалах  (по умолчанию 200ms(100us X 2000(0x07D0))) актуально для комманд CONNECT, DISCON, CLOSE, SEND, SEND_MAC, SEND_KEEP
#define W5200_RCR         (0x04)            // число повторов передачи  (по умолчанию 0x08 раз))
#define MAIN_WEB_TASK      0                // какой поток вебсервера является основным (поток в котором идет отправка MQTT и уведомлений) обычно 0
#define NEXTION_PORT         Serial1        // Аппаратный порт куда прицеплен дисплей
#define NEXTION_PORT_SPEED   9600           // Скорость порта, бод
#define NEXTION_UPDATE       5000           // Время обновления информации на дисплее Nextion (мсек)
#define NEXTION_BOOT_TIME    300            // Время для загрузки дисплея, если при сбросе дисплей не находится надо увеличить (мсек)
#define NEXTION_READ         50             // Время опроса дисплея Nextion (мсек) разбор входной очереди
#ifdef LCD2004
#undef KEY_ON_OFF
#define LCD_COLS				20			// Колонок на LCD экране
#define LCD_ROWS				4			// Строк на LCD экране
#define DISPLAY_UPDATE			2000           // Время обновления информации на дисплее (мсек)
#define KEY_CHECK_PERIOD		5              // ms
#define KEY_DEBOUNCE_TIME		50             // ms
#define DISPLAY_SETUP_TIMEOUT	600000         // ms
#define LCD_SetupFlag 			0x80000000
#define LCD_SetupMenuItems		6
#define LCD_MainScreenMaxItem	3				// 0..
#define LCD_SetupMenu_OnOff		0x100
#define LCD_SetupMenu_Relays	0x200
#define LCD_SetupMenu_Sensors	0x300
#define LCD_SetupMenu_Network	0x400
#define LCD_SetupMenu_UpdateFW	0x500
#define LCD_SetupMenu_Relays_Max 8
const char *LCD_SetupMenu[LCD_SetupMenuItems] = { "Exit", "On/Off", "Relays", "Sensors", "Safe Network", "Prepare FW update" };
const char LCD_Str_SetupInfo[] = "Long press OK - Exit";
const char LCD_Str_House[] = "House ";
const char LCD_Str_Boiler[] = "Boiler";
const char LCD_Str_Freq[] = "Freq. ";
const char LCD_Str_HP[] = "HeatPump";
const char LCD_Str_On[] = "ON";
const char LCD_Str_Off[] = "OFF";
const char LCD_Str_SafeNework[] = "OK - SafeNetwork";
const char LCD_Str_PrepareUpdate[] = "OK - Prepare update";
#endif
#define MODBUS_PORT_NUM      Serial2        // Аппаратный порт куда прицеплен Modbus
#define MODBUS_PORT_SPEED    9600           // Скорость порта куда прицеплен частотник и счетчик
#define MODBUS_PORT_CONFIG   SERIAL_8N1     // Конфигурация порта куда прицеплен частотник и счетчик
#define MODBUS_TIME_WAIT     2000           // Время ожидания захвата мютекса для modbus мсек
#define MODBUS_TIME_TRANSMISION 4           // Пауза (msec) между запросом и ответом по модбас было 4
#define MODBUS_TIMEOUT       100			// Таймаут ожидания ответа, мсек
#define MODBUS_MIN_TIME_BETWEEN_TRNS 50		// Минимальная пауза между транзакциями, мсек
#if RADIO_SENSORS_PORT == 2
	#define RADIO_SENSORS_SERIAL	Serial2	// Аппаратный порт
#elif RADIO_SENSORS_PORT == 3
	#define RADIO_SENSORS_SERIAL	Serial3	// Аппаратный порт
#endif
#define RADIO_LOST_TIMEOUT	40*60*1000		// через сколько считать, что связь потеряна с датчиком, мсек
#define RADIO_BAT_MIN_V		21				// Минимальное напряжение батарейки датчика, десятые V
#define FC_MODBUS_ADR      1             // Адрес частотного преобразователя на шине не должно совпадать SMD_MODBUS_ADR
#define FC_TIME_READ       4000UL       // Время опроса инвертора в мс (было 8)
#define FC_NUM_READ        5             // Число попыток чтения инвертора (подряд) по модбас до его останова ТН по ошибке
#define FC_DELAY_REPEAT    100           // мсек Время между ПОВТОРНЫМИ попытками чтения было 100
#define FC_DELAY_READ      10            // мсек Время между последовательными запросами было 20
#define FC_WRITE_READ      10            // мсек Время между последовательной записью
#define FC_ANALOG_RESOLUTION	8		// Bit (8..12)
#define DEFAULT_SDM_SPEED       2400      // Скорость в бодах для счетчика по умолчанию
#define DEFAULT_SDM_MODBUS_ADR  1         // Адрес счетчика на шине не должно совпадать с FC_MODBUS_ADR при программировании инвертор ОКЛЮЧИТЬ (адрес 1)
#define SDM_SPEED           2              // скорость счетчика в константах 0 = 2400 bps. 1 = 4800 bps. 2 = 9600 bps 5=1200 bps  Скорости обмена должны совпадать см MODBUS_PORT_SPEED
#define SDM_MODBUS_ADR      2              // Адрес счетчика на шине не должно совпадать с FC_MODBUS_ADR
#define SDM_READ_PERIOD     (10*1000)      // Время опроса счетчика в мск
#define SDM_NUM_READ        4              // Число попыток чтения счетчика (подряд) по модбас до его отключения (ошибка не генерится)
#define SDM_DELAY_REPEAD    100            // мсек Время между ПОВТОРНЫМИ попытками чтения  было 40 (меньше не имеет смысла - счетчик может не успеть)
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

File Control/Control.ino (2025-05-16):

/*
 * Copyright (c) 2016-2021 by Vadim Kulakov vad7@yahoo.com, vad711
 * &                       by Pavel Panfilov <firstlast2007@gmail.com> pav2000
 * "Народный контроллер" для тепловых насосов.
 * Данное програмноое обеспечение предназначено для управления
 * различными типами тепловых насосов для отопления и ГВС.
 *
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
 * This file is distributed in the hope that it will be useful,
 * but WITHOUT ANY WARRANTY; without even the implied warranty of
 * MERCHANTABILITY or FITNESS FOR A PARTICULAR PURPOSE.See the
 * GNU General Public License for more details.
 */
// Последние версии
// https://github.com/vad7/ControlHeatPump - последняя стабильная версия
// Архивные ссылки
// https://github.com/vad7/Arduino-DUE-WireSam  библиотеки доработанные vad711 при релизе добавляются в архив

#include "Arduino.h"
#include "Constant.h"                       // Должен быть первым !!!! кое что берется в стандартных либах для настройки либ, Config.h входит в него

#include <WireSam.h>                        // vad711 доработанная библиотека https://github.com/vad7/Arduino-DUE-WireSam
#include <DS3232.h>                         // vad711 Работа с часами i2c - используются при выключении питания. модифицированная https://github.com/vad7/Arduino-DUE-WireSam
#include <extEEPROM.h>                      // vad711 Работа с eeprom и fram i2c библиотека доработана для DUE!!! https://github.com/vad7/Arduino-DUE-WireSam

#include <SPI.h>                            // SPI - стандартная
#include "SdFat.h"                          // SdFat - модифицированная
#include "FreeRTOS_ARM.h"                   // модифицированная
#include <rtc_clock.h>                      // работа со встроенными часами  Это основные часы!!!
#include <ModbusMaster.h>                   // Используется МОДИФИЦИРОВАННАЯ для омрона мх2 либа ModbusMaster https://github.com/4-20ma/ModbusMaster

// Глубоко переделанные библиотеки
#include <Ethernet.h>                       // Ethernet - модифицированная
#include <Dns.h>                            // DNS - модифицированная
#include <SerialFlash.h>                    // Либа по работе с spi флешом как диском

#include "Hardware.h"
#include "HeatPump.h"
#include "Nextion.h"
#include "Message.h"
#include "Information.h"
#include "MQTT.h"
#include "Statistics.h"
#include "LCD2004.h"

void vUpdateStepperEEV(void *);
#include "StepMotor.h"

// Мютексы блокираторы железа
SemaphoreHandle_t xModbusSemaphore;                 // Семафор Modbus, инвертор запас на счетчик
SemaphoreHandle_t xWebThreadSemaphore;              // Семафор потоки вебсервера,  деление сетевой карты
SemaphoreHandle_t xI2CSemaphore;                    // Семафор шины I2C, часы, память, мастер OneWire
SemaphoreHandle_t xSPISemaphore;                    // Семафор шины SPI  сетевая карта, память. SD карта // пока не используется
SemaphoreHandle_t xLoadingWebSemaphore;             // Семафор загрузки веб морды в spi память
uint16_t lastErrorFreeRtosCode;                     // код последней ошибки операционки нужен для отладки
uint32_t startSupcStatusReg;                        // Состояние при старте SUPC Supply Controller Status Register - проверяем что с питание


#if defined(W5500_ETHERNET_SHIELD)                  // Задание имени чипа для вывода сообщений
  const char nameWiznet[] ={"W5500"};
#elif defined(W5200_ETHERNET_SHIELD)
  const char nameWiznet[] ={"W5200"};
#else
  const char nameWiznet[] ={"W5100"};
#endif

// Глобальные переменные
EthernetServer server1(80);                         // сервер
#ifdef MQTT
EthernetClient ethClient(W5200_SOCK_SYS);           // для MQTT
#endif

#ifdef RADIO_SENSORS
void check_radio_sensors(void);
void radio_sensor_send(char *cmd);
#endif

#ifdef MQTT                                 // признак использования MQTT
#include <PubSubClient.h>                   // передаланная под многозадачность  http://knolleary.net
PubSubClient w5200_MQTT(ethClient);  	    // клиент MQTT
#endif

// I2C eeprom Размер в килобитах, число чипов, страница в байтах, адрес на шине, тип памяти:
extEEPROM eepromI2C(I2C_SIZE_EEPROM,I2C_MEMORY_TOTAL/I2C_SIZE_EEPROM,I2C_PAGE_EEPROM,I2C_ADR_EEPROM,I2C_FRAM_MEMORY);
#ifdef USE_RC_CLOCK_SOURCE
RTC_clock rtcSAM3X8(RC);                                               // Внутренние часы, используется внутренний RC генератор
#else
RTC_clock rtcSAM3X8(XTAL);                                               // Внутренние часы, используется часовой кварц
#endif
DS3232  rtcI2C;                                                          // Часы 3231 на шине I2C
static Journal  journal;                                                 // системный журнал, отдельно т.к. должен инициализоваться с начала старта
static HeatPump HP;                                                      // Класс тепловой насос (в констукторе плохо проходит инициализация пинов????)
static devModbus Modbus;                                                 // Класс модбас - управление инвертором
SdFat card;                                                              // Карта памяти
#ifdef NEXTION   
Nextion myNextion;                                                     // Дисплей
#endif

// Use the Arduino core to set-up the unused USART2 on Serial4 (without serial events)
#ifdef USE_SERIAL4
RingBuffer rx_buffer5;
RingBuffer tx_buffer5;
USARTClass Serial4(USART2, USART2_IRQn, ID_USART2, &rx_buffer5, &tx_buffer5);
//void serialEvent4() __attribute__((weak));
//void serialEvent4() { }
void USART2_Handler(void)   // Interrupt handler for UART2
{
	Serial4.IrqHandler();     // In turn calls on the Serial2 interrupt handler
}
#endif


// Структура для хранения одного сокета, нужна для организации многопотоковой обработки
#define fABORT_SOCK   0                     // флаг прекращения передачи (произошел сброс сети)
#define fUser         1                     // Признак идентификации как обычный пользователь (нужно подменить файл меню)

struct type_socketData
  {
    EthernetClient client;                  // Клиент для работы с потоком
    byte inBuf[W5200_MAX_LEN];              // буфер для работы с w5200 (входной запрос)
    char *inPtr;                            // указатель в входном буфере с именем файла или запросом (копирование не делаем)
    char outBuf[3*W5200_MAX_LEN];           // буфер для формирования ответа на запрос и чтение с карты
    int8_t sock;                            // сокет потока -1 свободный сокет
    uint8_t flags;                          // Флаги состояния потока
    uint16_t http_req_type;                 // Тип запроса
  };
static type_socketData Socket[W5200_THREAD];   // Требует много памяти 4*W5200_MAX_LEN*W5200_THREAD=24 кб

// Установка вачдога таймера вариант vad711 - адаптация для DUE 1.6.11
// WDT_TIME период Watchdog таймера секунды но не более 16 секунд!!! ЕСЛИ WDT_TIME=0 то Watchdog будет отключен!!!
volatile unsigned long ulHighFrequencyTimerTicks;   // vad711 - адаптация для DUE 1.6.11
void watchdogSetup(void)
{
#if WDT_TIME == 0
	watchdogDisable();
#else 
	watchdogEnable(WDT_TIME * 1000);
#endif
}

__attribute__((always_inline)) inline void _delay(int t) // Функция задержки (мсек) в зависимости от шедулера задач FreeRtos
{
  if(xTaskGetSchedulerState() == taskSCHEDULER_RUNNING) vTaskDelay(t/portTICK_PERIOD_MS);
  else delay(t);
}

// Захватить семафор с проверкой, что шедуллер работает
BaseType_t SemaphoreTake(QueueHandle_t xSemaphore, TickType_t xBlockTime)
{
	if(xTaskGetSchedulerState() != taskSCHEDULER_RUNNING) return pdTRUE;
	else {
		for(;;) {
			if(xSemaphoreTake(xSemaphore, 0) == pdTRUE) return pdTRUE;
			if(!xBlockTime--) break;
			vTaskDelay(1/portTICK_PERIOD_MS);
		}
		return pdFALSE;
	}
}

// Освободить семафор с проверкой, что шедуллер работает
inline void SemaphoreGive(QueueHandle_t xSemaphore)
{
	if(xTaskGetSchedulerState() == taskSCHEDULER_RUNNING) xSemaphoreGive(xSemaphore);
}

// Остановить шедулер задач, возврат 1, если получилось
uint8_t TaskSuspendAll(void) {
	if(xTaskGetSchedulerState() == taskSCHEDULER_RUNNING) {
		vTaskSuspendAll(); // запрет других задач
		return 1;
	}
	return 0;
}

void vWeb0(void *) __attribute__((naked));
void vWeb1(void *) __attribute__((naked));
void vWeb2(void *) __attribute__((naked));
void vWeb3(void *) __attribute__((naked));
void vReadSensor(void *) __attribute__((naked));
void vUpdate( void * ) __attribute__((naked));
void vUpdateEEV(void *) __attribute__((naked));
void vUpdateStepperEEV(void *) __attribute__((naked));
void vUpdateCommand(void *) __attribute__((naked));
void vServiceHP(void *) __attribute__((naked));

void setup() {
	// 1. Инициализация
	// Баг разводки дуе (вероятность). Есть проблема с инициализацией spi.  Ручками прописываем
	// https://groups.google.com/a/arduino.cc/forum/#!topic/developers/0PUzlnr7948
	// http://forum.arduino.cc/index.php?topic=243778.0;nowap
	pinMode(PIN_SPI_SS0,INPUT_PULLUP);          // Eth Pin 77
	pinMode(PIN_SPI_SS1,INPUT_PULLUP);          // SD Pin  87
	pinMode(PIN_SPI_CS_SD,INPUT_PULLUP);        // сигнал CS управление SD картой
	pinMode(PIN_SPI_CS_W5XXX,INPUT_PULLUP);     // сигнал CS управление сетевым чипом

#ifdef SPI_FLASH
	pinMode(PIN_SPI_CS_FLASH,INPUT_PULLUP);     // сигнал CS управление чипом флеш памяти
	pinMode(PIN_SPI_CS_FLASH,OUTPUT);           // сигнал CS управление чипом флеш памяти
#endif
	SPI_switchAllOFF();                         // Выключить все устройства на SPI
	// Отключить питание (VUSB) на Native USB
	Set_bits(UOTGHS->UOTGHS_CTRL, UOTGHS_CTRL_VBUSHWC);
	PIO_Configure(PIOB, PIO_OUTPUT_0, PIO_PB10A_UOTGVBOF, PIO_DEFAULT);
	PIOB->PIO_CODR = PIO_PB10A_UOTGVBOF; // =0
	//

#ifdef POWER_CONTROL                        // Включение питания платы если необходимо НАДП здесь, иначе I2C память рабоать не будет
	pinMode(PIN_POWER_ON,OUTPUT);
	digitalWriteDirect(PIN_POWER_ON, LOW);
#endif

	// Борьба с зависшими устройствами на шине  I2C (в первую очередь часы) неудачный сброс
	Recover_I2C_bus();
	delay(1);

	// Настройка сервисных выводов
	pinMode(PIN_KEY1, INPUT_PULLUP);        // Кнопка 1
	pinMode(PIN_BEEP, OUTPUT);              // Выход на пищалку
	pinMode(PIN_LED_OK, OUTPUT);            // Выход на светодиод мигает 0.5 герца - ОК  с частотой 2 герца ошибка
	digitalWriteDirect(PIN_BEEP,LOW);       // Выключить пищалку
	digitalWriteDirect(PIN_LED_OK,HIGH);    // Выключить светодиод

	// 2. Инициализация журнала
	uint8_t b;
	uint8_t ret = eepromI2C.read(I2C_COUNT_EEPROM, &b, 1);
	if(ret == 0 && b != I2C_COUNT_EEPROM_HEADER && b != 0xFF) {
#ifndef TEST_BOARD
		if(b == 0xAA) {
			if(!eepromI2C.read(I2C_SETTING_EEPROM + 2 + 1, &b, 1) && b < 147) goto xRewriteHeader;
		}
#endif
		ret = 0xFF;
	}
#ifndef DEBUG
	if(ret)
#endif
#ifndef DEBUG_NATIVE_USB
	SerialDbg.begin(UART_SPEED);                   // Если надо инициализировать отладочный порт
#endif
#ifdef LCD2004
	lcd.begin(LCD_COLS, LCD_ROWS); // Setup: cols, rows
	lcd.print("HeatPump v");
	lcd.print(VERSION);
	lcd.setCursor(0, 1);
	lcd.print("(C) vad7@yahoo.com");
	lcd.setCursor(0, 2);
	lcd.print("CFG: ");
	lcd.print(CONFIG_NAME);
	lcd.setCursor(0, 3);
	lcd.print("Loading...");
#endif
	while(ret) {
		SerialDbg.print("Wrong I2C EEPROM or setup, press KEY[D");
		SerialDbg.print(PIN_KEY1);
		SerialDbg.println("] to continue...");
		if(!digitalReadDirect(PIN_KEY1)) {
			WDT_Restart(WDT);
#ifndef TEST_BOARD
xRewriteHeader:
#endif
			b = I2C_COUNT_EEPROM_HEADER;
			ret = eepromI2C.write(I2C_COUNT_EEPROM, &b, 1);
			if(ret) {
				SerialDbg.print("Error ");
				SerialDbg.print(ret);
				SerialDbg.println(" write to EEPROM!");
#ifdef TEST_BOARD
				break;
#endif
			} else SerialDbg.println("Wait...");
			while(1) ;
		}
		for(uint8_t i = 0; i < 1000 / TIME_LED_ERR; i++) {
			digitalWriteDirect(PIN_BEEP, i & 1);
			digitalWriteDirect(PIN_LED_OK, i & 1);
			delay(TIME_LED_ERR);
		}
	}
#ifdef TEST_BOARD
	//_delay(1); // Если зависает при загрузке (START...START...) - включить или выключить эту строку
#endif
	journal.Init();
#ifdef POWER_CONTROL
	delay(200);  // Не понятно но без нее иногда на старте срабатывает вачдог.  возможно проблема с буфером
#endif
#ifdef DEMO
	journal.jprintf("DEMO - DEMO - DEMO - DEMO - DEMO - DEMO - DEMO\n");
#endif
#ifdef TEST_BOARD
	journal.jprintf("\n---> TEST BOARD!!!\n\n");
#endif
	journal.jprintf("Config: %s\n", CONFIG_NAME);
	journal.jprintf("Firmware version: %s\n", VERSION);
	showID();                                                                  // информация о чипе
	getIDchip((char*)Socket[0].inBuf);
	journal.jprintf("Chip ID SAM3X8E: %s\n", Socket[0].inBuf);// информация об серийном номере чипа
	if(GPBR->SYS_GPBR[0] & 0x80000000) GPBR->SYS_GPBR[0] = 0; else GPBR->SYS_GPBR[0] |= 0x80000000; // очистка старой причины
	lastErrorFreeRtosCode = GPBR->SYS_GPBR[0] & 0x7FFFFFFF;         // Сохранение кода ошибки при страте (причину перегрузки)
	journal.jprintf("Last reason for reset SAM3x: %s\n", ResetCause());
	journal.jprintf("Last FreeRTOS task + error: 0x%04x", lastErrorFreeRtosCode);
	if(GPBR->SYS_GPBR[4]) journal.jprintf(" (%d)", GPBR->SYS_GPBR[4]);
	if(GPBR->SYS_GPBR[5]) journal.jprintf(" Web(%d)", GPBR->SYS_GPBR[5]);
	journal.jprintf("\n");

#ifdef PIN_LED1                            // Включение (точнее индикация) питания платы если необходимо
	pinMode(PIN_LED1,OUTPUT);
	digitalWriteDirect(PIN_LED1, HIGH);
#endif
#ifdef POWER_CONTROL
	journal.jprintf("Power +5V, +3.3V on board: ON\n");
#endif

	SupplyMonitorON(SUPC_SMMR_SMTH_3_0V);           // включение монитора питания

#ifdef DRV_EEV_L9333                     // Контроль за работой драйвера ЭРВ
	pinMode(PIN_STEP_DIAG,INPUT_PULLUP);
	journal.jprintf("Control EEV driver L9333: ON \n");
#endif
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
void loop() {}

//  З А Д А Ч И -------------------------------------------------
// Это и есть поток с минимальным приоритетом измеряем простой процессора
//extern "C" 
//{
static bool Error_Beep_confirmed = false;

extern "C" void vApplicationIdleHook(void)  // FreeRTOS expects C linkage
{
	static unsigned long countLED = 0;
	static unsigned long countBeep = 0;

	WDT_Restart(WDT);                                                            // Сбросить вачдог
	register unsigned long ticks = GetTickCount();
//	static unsigned long cpu_idle_max_count = 0; // 1566594 // максимальное значение счетчика, вычисляется при калибровке и соответствует 100% CPU idle
//	static unsigned long ulIdleCycleCount = 0;
//	ulIdleCycleCount++;                                                          // приращение счетчика
//	if(ticks - countLastTick >= 3000)		// мсек
//	{
//		countLastTick = ticks;                            // расчет нагрузки
//		if(ulIdleCycleCount > cpu_idle_max_count) cpu_idle_max_count = ulIdleCycleCount; // это калибровка запоминаем максимальные значения
//		HP.CPU_IDLE = (100 * ulIdleCycleCount) / cpu_idle_max_count;              // вычисляем текущую загрузку
//		ulIdleCycleCount = 0;
//	}
	// Светодиод мигание в зависимости от ошибки и подача звукового сигнала при ошибке
	if(HP.get_errcode() != OK) {          // Ошибка
		if(ticks - countLED > TIME_LED_ERR) {
			digitalWriteDirect(PIN_LED_OK, !digitalReadDirect(PIN_LED_OK));
			countLED = ticks;
		}
		if(HP.get_Beep() && !Error_Beep_confirmed && ticks - countBeep > TIME_BEEP_ERR) {
			digitalWriteDirect(PIN_BEEP, !digitalReadDirect(PIN_BEEP)); // звуковой сигнал
			countBeep = ticks;
		}
	} else if(ticks - countLED > TIME_LED_OK) {   // Ошибок нет и время пришло
		Error_Beep_confirmed = false;
		digitalWriteDirect(PIN_BEEP, LOW);
		digitalWriteDirect(PIN_LED_OK, !digitalReadDirect(PIN_LED_OK));
		countLED = ticks;
	}
	pmc_enable_sleepmode(0);
}

// --------------------------- W E B ------------------------
// Задача обслуживания web сервера
// Сюда надо пихать все что связано с сетью иначе конфликты не избежны
// Здесь также обслуживается посылка уведомлений MQTT
// Первый поток веб сервера - дополнительно нагружен различными сервисами
void vWeb0(void *)
{ //const char *pcTaskName = "Web server is running\r\n";
	static unsigned long timeResetW5200 = 0;
	static unsigned long thisTime;
	static unsigned long resW5200 = 0;
	static unsigned long iniW5200 = 0;
	static unsigned long pingt = 0;
#ifdef HTTP_LowConsumeRequest
	static uint16_t RepeatLowConsumeRequest = 0;
#endif
	static boolean network_last_link = true;
#ifdef MQTT
	static unsigned long narmont=0;
	static unsigned long mqttt=0;
#endif
#ifdef WEATHER_FORECAST
	static uint8_t WF_Day = 0;
#endif
#if defined(HTTP_MAP_RELAY_MAX) && defined(HTTP_MAP_Server)
	static uint32_t daily_http_time = 0;
#endif
#ifdef WATTROUTER
	memset(WR_LoadRun, 0, sizeof(WR_LoadRun));
	memset(WR_SwitchTime, 0, sizeof(WR_SwitchTime));
	for(uint8_t i = 0; i < WR_NumLoads; i++) {
		if(WR_Load_pins[i] > 0) pinMode(WR_Load_pins[i], OUTPUT);
	}
 #ifdef PIN_WR_Boiler_Substitution
	pinMode(PIN_WR_Boiler_Substitution, OUTPUT);
 #endif
#ifdef WR_CHECK_Vbat_INSTEAD_OF_MPPT_SIGN
	if(WR_Read_MAP() == -32768) journal.jprintf("WR: Error read Ubuf\n");
	journal.jprintf("WattRouter started, Ubuf=%.1d\n", WR_MAP_Ubuf);
#else
	journal.jprintf("WattRouter started\n");
#endif
#endif

	HP.timeNTP = thisTime = xTaskGetTickCount();        // В первый момент не обновляем
#ifndef WR_PowerMeter_Modbus
	Web0_FreqTime = thisTime;
#endif
	for(;;)
	{
		#define WEB_SERVER_MAIN_TASK() {\
			/*WEB_STORE_DEBUG_INFO(1);*/\
			web_server(MAIN_WEB_TASK);\
			/*WEB_STORE_DEBUG_INFO(2);*/\
			vTaskDelay(TIME_WEB_SERVER / portTICK_PERIOD_MS);\
		}
		WEB_SERVER_MAIN_TASK();

		// СЕРВИС: Этот поток работает на любых настройках, по этому сюда ставим работу с сетью
		boolean active = true;   // ФЛАГ Одно дополнительное действие за один цикл - распределяем нагрузку, если действие проделано то active = false и новый цикл
#ifdef WR_PowerMeter_Modbus		// Синхронизируемся с чтением счетчика - сразу после
		if(WR_PowerMeter_New) {
			WR_PowerMeter_New = false;
#else
		if(xTaskGetTickCount() - Web0_FreqTime > WEB0_FREQUENT_JOB_PERIOD) {
			Web0_FreqTime = xTaskGetTickCount();
#endif
			active = HP.message.sendMessage();   // Отработать отсылку сообщений (внутри скрыта задержка после включения)
#ifdef HTTP_LowConsumeRequest
			if(active) {
				if(GETBIT(HP.Option.flags, fBackupPower) != Request_LowConsume || (RepeatLowConsumeRequest && --RepeatLowConsumeRequest == 0)) {
					strcpy(Socket[MAIN_WEB_TASK].outBuf, HTTP_LowConsumeRequest);
					_itoa(GETBIT(HP.Option.flags, fBackupPower), Socket[MAIN_WEB_TASK].outBuf + sizeof(HTTP_LowConsumeRequest)-1);
					int err = Send_HTTP_Request(HTTP_LowConsumeServer, WebSec_Microart.hash, Socket[MAIN_WEB_TASK].outBuf, false);
					if(err != -2000000000) {
						if(err > -2000000000) Request_LowConsume = GETBIT(HP.Option.flags, fBackupPower);
						else RepeatLowConsumeRequest = (uint16_t)(HTTP_REQUEST_ERR_REPEAT * 1000 / WEB0_OTHER_JOB_PERIOD + 1);
					}
					active = false;
				}
			}
#endif
#ifdef WATTROUTER
			if(!active) {
				WEB_SERVER_MAIN_TASK();	/////////////////////////////////////// Выполнить задачу веб сервера
				active = true;
			}
			if((GETBIT(WR.Flags, WR_fActive) || WR.PWM_FullPowerTime || WR_Refresh) /*&& HP.get_State() == pWORK_HP*/) {
				while(1) {
					static uint8_t skip_next_small_increase = 0;
					if(skip_next_small_increase) skip_next_small_increase--;
#ifdef PWM_CALC_POWER_ARRAY
					if(GETBIT(PWM_CalcFlags, PWM_fCalcNow)) break;
#endif
					uint8_t nopwr = GETBIT(WR.Flags, WR_fActive) && (GETBIT(HP.Option.flags, fBackupPower) || HP.NO_Power
#ifdef WR_PowerMeter_Modbus
									|| WR_Error_Read_PowerMeter > WR_Error_Read_PowerMeter_Max
#endif
									 );
#ifdef WR_NEXTION_FULL_SUN
					int8_t mppt = -1;
					if(GETBIT(WR_WorkFlags, WR_fWF_Read_MPPT) || WR_LastSunPowerOutCnt == 0 || nopwr) {
						mppt = WR_Check_MPPT();				// Чтение солнечного контроллера
						SETBIT0(WR_WorkFlags, WR_fWF_Read_MPPT);
						WEB_SERVER_MAIN_TASK();	/////////////////////////////////////// Выполнить задачу веб сервера
					}
#endif
					// Выключить все
					if(nopwr) {
						WR_Refresh |= WR_Loads;
						// При отсутствии питания мониторим напряжение на АКБ (не должно быть ниже буферного - дельта)
						int16_t Vd;
#if defined(HTTP_MAP_Read_MAP) && defined(WR_NOPWR_READ_MAP_INSTEAD_OF_MPPT)
						active = false;
						Vd = WR_Read_MAP();
#else
						if(WR_MAP_Ubat) Vd = WR_MAP_Ubuf - WR_MAP_Ubat; else Vd = -32768;
#endif //HTTP_MAP_Read_MAP
						if(Vd != -32768) {
							if(Vd <= WR.DeltaUbatmin) { // Можно нагружать
#ifdef WR_Load_pins_Boiler_INDEX
								if(HP.sTemp[TBOILER].get_Temp() <= HP.Prof.Boiler.WR_Target && GETBIT(WR_Loads, WR_Load_pins_Boiler_INDEX)) { // Нужно греть бойлер
									if(Vd <= 0) { // Можно увеличивать нагрузку
										if(WR_LoadRun[WR_Load_pins_Boiler_INDEX] > 0 || HP.sTemp[TBOILER].get_Temp() <= HP.Prof.Boiler.WR_Target - WR_Boiler_Hysteresis) {
											if(GETBIT(WR.PWM_Loads, WR_Load_pins_Boiler_INDEX)) WR_Change_Load_PWM(WR_Load_pins_Boiler_INDEX, WR.LoadAdd);
											else WR_Switch_Load(WR_Load_pins_Boiler_INDEX, 1);
											Vd = WR_NO_POWER_WORK_DELTA_Uacc - 1; // Выключить остальные нагрузки
										}
										goto xNOPWR_OtherLoad;
									} else if(Vd > WR_NO_POWER_WORK_DELTA_Uacc) { // Уменьшаем или выключаем
										if(GETBIT(WR.PWM_Loads, WR_Load_pins_Boiler_INDEX)) WR_Change_Load_PWM(WR_Load_pins_Boiler_INDEX, -WR.LoadAdd);
									}
								} else { // Другая нагрузка
									if(WR_LoadRun[WR_Load_pins_Boiler_INDEX] > 0) {
										if(GETBIT(WR.PWM_Loads, WR_Load_pins_Boiler_INDEX)) WR_Change_Load_PWM(WR_Load_pins_Boiler_INDEX, -32768);
										else WR_Switch_Load(WR_Load_pins_Boiler_INDEX, 0);
									}
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

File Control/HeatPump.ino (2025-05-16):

/*
 * Copyright (c) 2016-2022 by Vadim Kulakov vad7@yahoo.com, vad711
 * &                       by Pavel Panfilov <firstlast2007@gmail.com> pav2000
 * "Народный контроллер" для тепловых насосов.
 * Данное програмное обеспечение предназначено для управления
 * различными типами тепловых насосов для отопления и ГВС.
 *
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
 * This file is distributed in the hope that it will be useful,
 * but WITHOUT ANY WARRANTY; without even the implied warranty of
 * MERCHANTABILITY or FITNESS FOR A PARTICULAR PURPOSE.See the
 * GNU General Public License for more details.
 */
// --------------------------------------------------------------------------------
// Описание базового класса для работы Теплового Насоса  ==false
// --------------------------------------------------------------------------------
#include "HeatPump.h"

// Булевые константы для упрощения читаемости кода (используются только в этом файле)
const boolean _stop =  true;   // Команда останов ТН
const boolean _wait =  false;  // Команда перевода в режим ожидания ТН
const boolean _start = true;   // Команда запуска ТН
const boolean _resume = false;  // Команда возобновления работы ТН
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

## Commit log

2022-12-04 Плата НК версии 1.2 - Gerber, BOM, Pick&Place
    [Project_Arduino DUE shield - BOM.csv, Project_Arduino DUE shield - PickAndPlace_Board.csv]
2025-05-16 Версия 1.196 cо схемой и гербером платы
    [PriceCalc.xlsx, Project_Arduino DUE shield - BOM.csv, Project_Arduino DUE shield - BOM_DS3231-SOIC16.csv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]
2025-05-16 Версия 1.196 cо схемой, gerber, BOM платы
